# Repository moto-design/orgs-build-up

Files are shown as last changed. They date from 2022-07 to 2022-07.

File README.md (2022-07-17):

# ORGS Build Up

Build up of the ORGS BMW R100GS motorcycle.

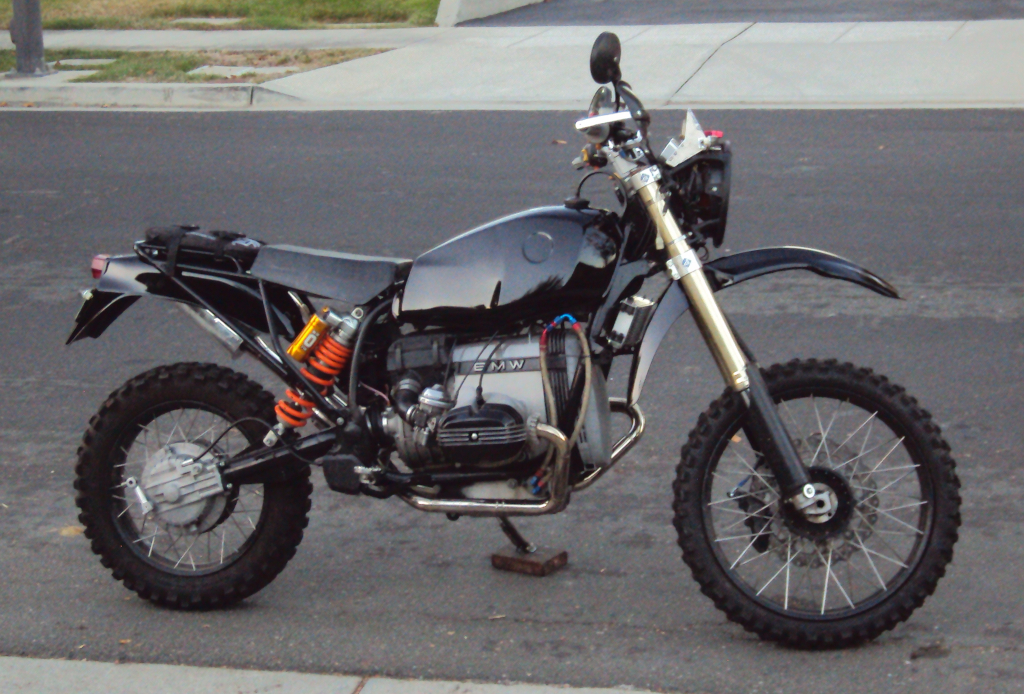
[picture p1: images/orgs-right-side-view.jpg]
ORGS


## Licence & Usage

All files in the [ORGS Build Up Project](https://github.com/moto-design/orgs-build-up), unless
otherwise noted, are covered by the
[Fabricators Design License](https://github.com/moto-design/orgs-build-up/blob/master/fabricators-design-license.txt).
The text of the license describes what usage is allowed.

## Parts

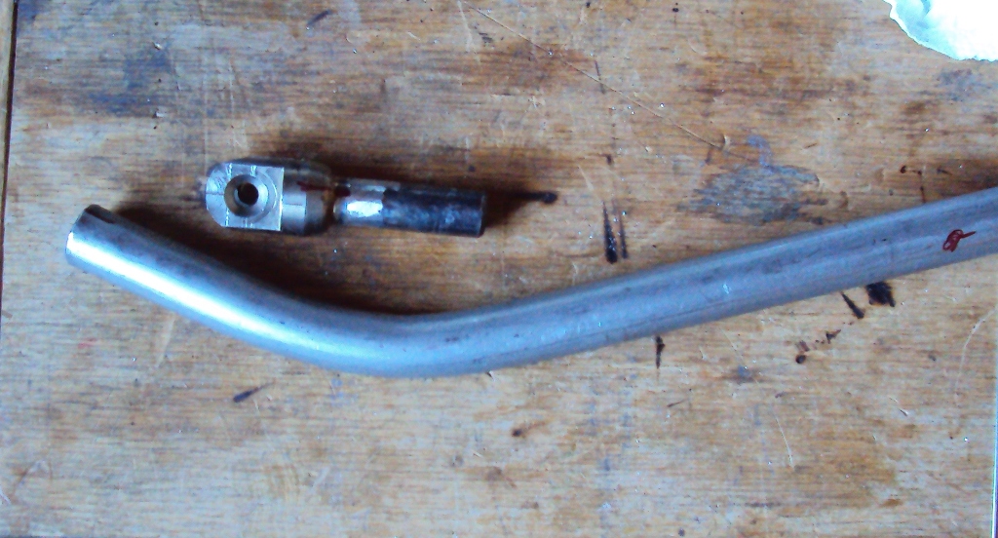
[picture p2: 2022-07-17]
images/50-sidestand/stainless-parts.jpg

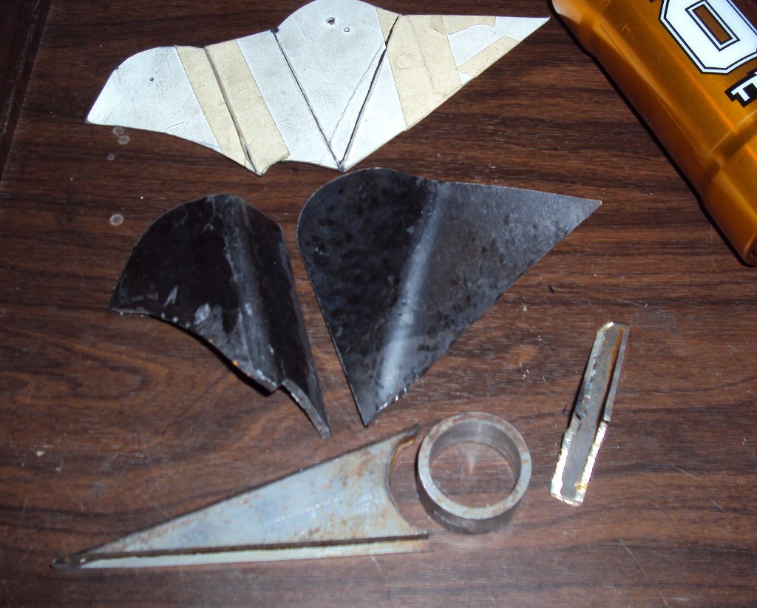
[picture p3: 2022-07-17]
images/32-shock-mounts/mount-parts.jpg

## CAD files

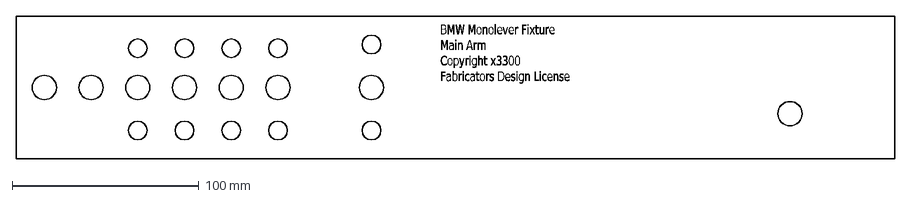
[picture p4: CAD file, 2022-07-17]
images/28-swingarm-fixture/main-arm.dxf
BMW\~Monolever\~Fixture Main\~Arm Copyright\~x3300 Fabricators\~Design\~License

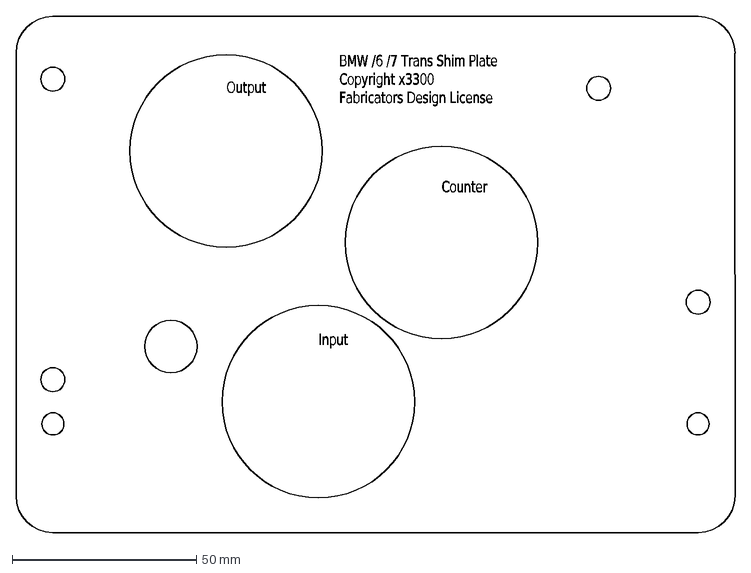
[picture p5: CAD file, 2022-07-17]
images/23-trans-rebuild/bmw-trans-shim-plate.dxf
Input
Counter
Output
BMW\~/6\~/7\~Trans\~Shim\~Plate Copyright\~x3300 Fabricators\~Design\~License

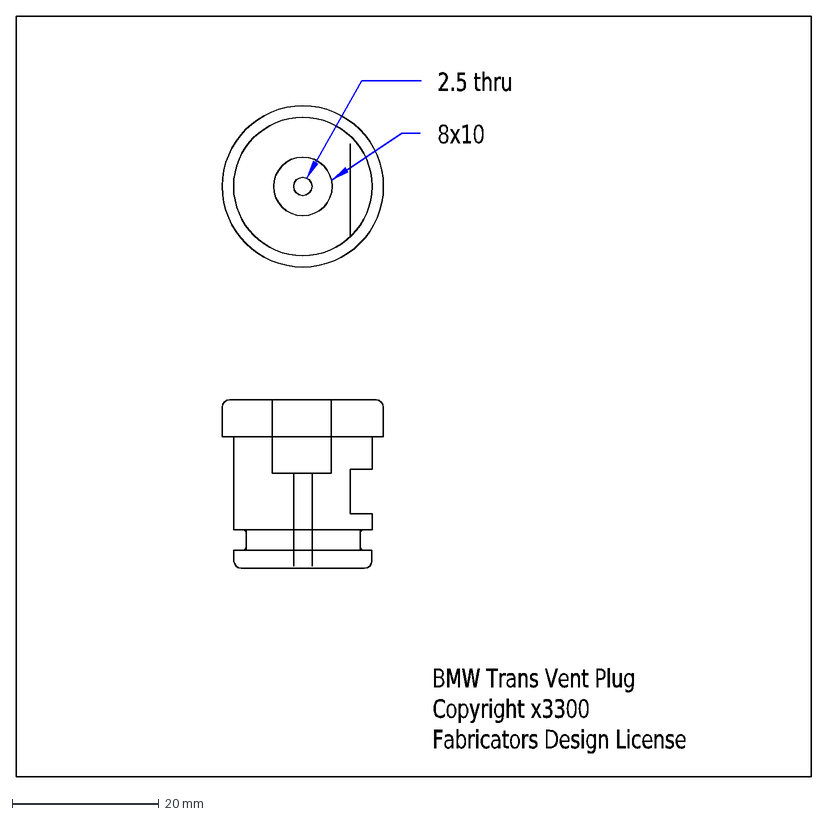
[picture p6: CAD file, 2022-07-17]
images/24-trans-vent/bmw-trans-vent.dxf
8x10
2.5\~thru
BMW\~Trans\~Vent\~Plug Copyright\~x3300 Fabricators\~Design\~License

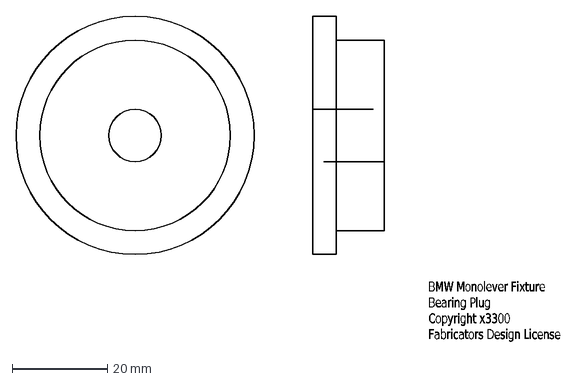
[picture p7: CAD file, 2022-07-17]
images/28-swingarm-fixture/bearing-plug.dxf
BMW\~Monolever\~Fixture Bearing\~Plug Copyright\~x3300 Fabricators\~Design\~License

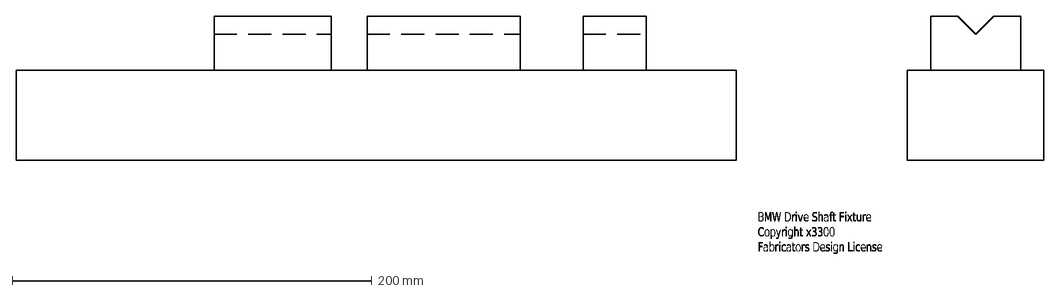
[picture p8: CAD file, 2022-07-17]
images/30-shaft-extension/shaft-fixture.dxf
BMW\~Drive\~Shaft\~Fixture Copyright\~x3300 Fabricators\~Design\~License

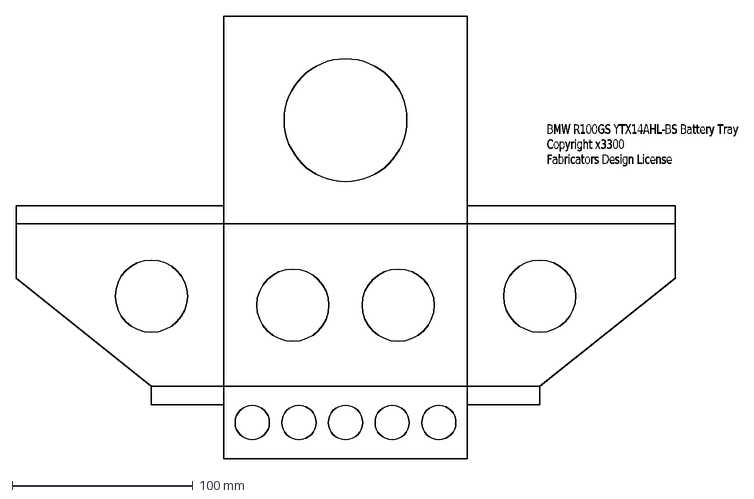
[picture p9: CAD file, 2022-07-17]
images/33-battery-tray/battery-tray.dxf
BMW\~R100GS\~YTX14AHL-BS\~Battery\~Tray Copyright\~x3300 Fabricators\~Design\~License

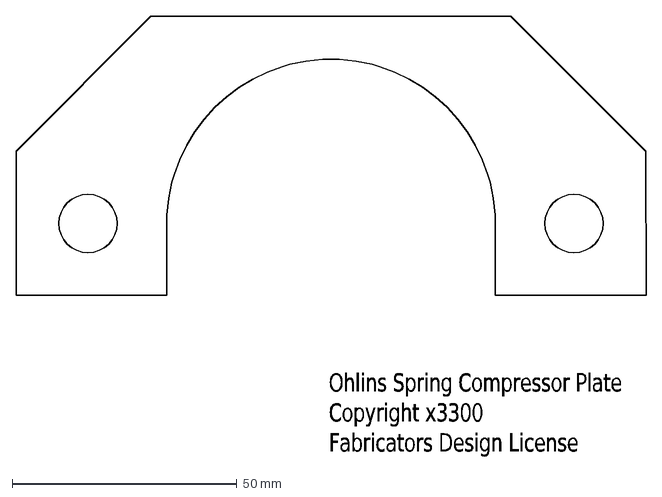
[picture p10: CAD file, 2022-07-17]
images/34-rear-spring/ohlins-plate.dxf
Ohlins\~Spring\~Compressor\~Plate Copyright\~x3300 Fabricators\~Design\~License

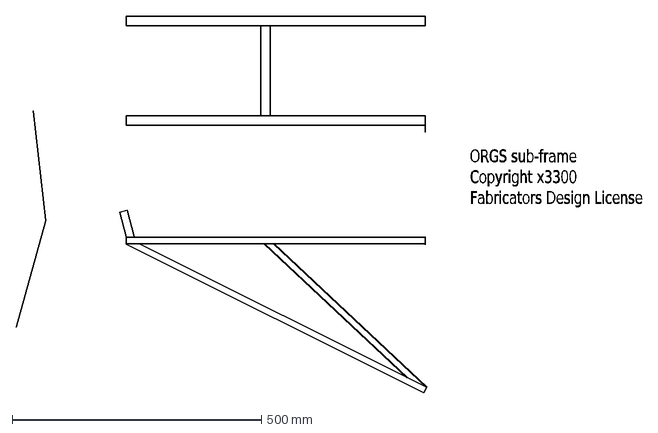
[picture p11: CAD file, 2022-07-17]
images/35-subframe/subframe.dxf
ORGS\~sub-frame Copyright\~x3300 Fabricators\~Design\~License

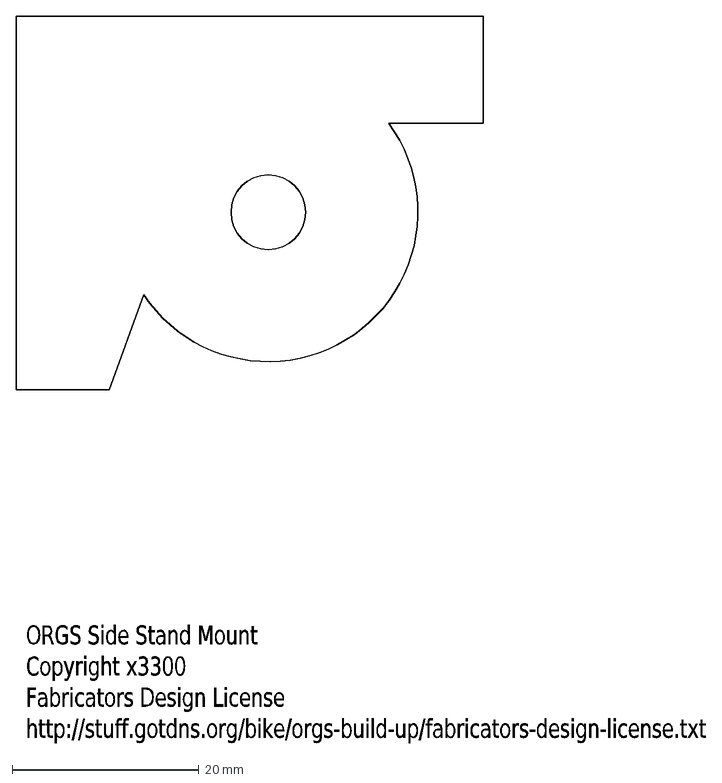
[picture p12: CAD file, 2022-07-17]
images/50-sidestand/side-stand-mount.dxf
ORGS Side Stand Mount Copyright x3300 Fabricators Design License http://stuff.gotdns.org/bike/orgs-build-up/fabricators-design-license.txt

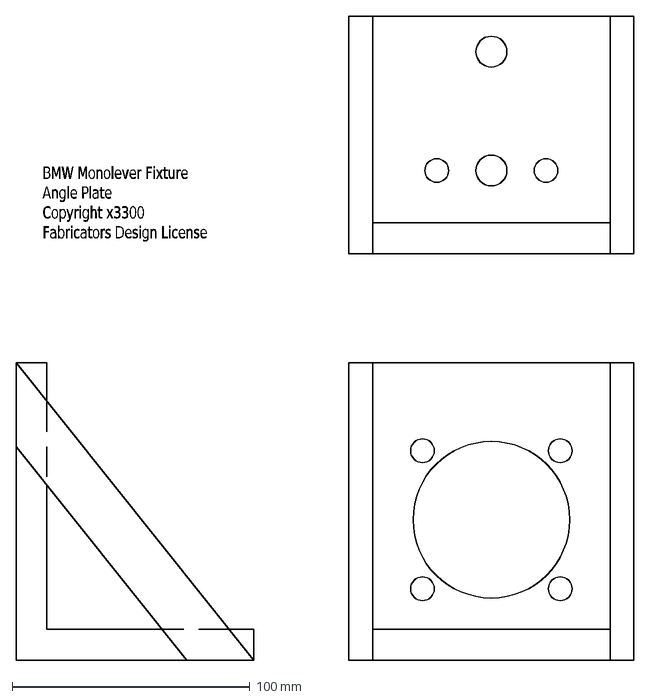
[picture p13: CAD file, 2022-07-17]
images/28-swingarm-fixture/angle-plate.dxf
BMW\~Monolever\~Fixture Angle\~Plate Copyright\~x3300 Fabricators\~Design\~License

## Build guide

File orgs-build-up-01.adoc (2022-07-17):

:url-bmw-frame-gussets: https://www.advrider.com/f/threads/bmw-frame-gussets.638795/
:url-frame-gussets-svg: https://github.com/moto-design/bmw-frame-gussets

:imagesdir: images
:linkattrs:

:notitle:
:nofooter:

= ORGS Build Up - Page 1

[big]*The ORGS Build Up Project*

*Page 1*

*x3300, Mar 6, 2010:*

Hi everyone,

I have really enjoyed the stories of other airhead bike build up projects, so will be posting mine, the build up of ORGS my Off-Road GS here.

I have a good general idea of what I want, but you'll have to follow along as the plan in my head unfolds. My intention is for ORGS to be a bike I can take on the highway and ride all day long for several days to get to a destination, say Moab, Baja, or Copper Canyon, spend a week or so doing some hard riding on unmaintained back roads, then make it back. I want it to be able to take a wipeout without a lot of damage, or cost to repair. That was a drawback of my GSPD. Windscreens, body panels, handle bars, etc. break and cost a lot.

As a base to start with I have bought this '92 GS with 27,000 miles:

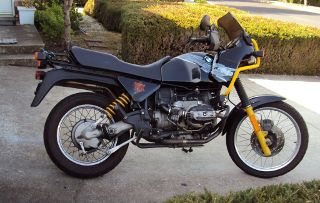
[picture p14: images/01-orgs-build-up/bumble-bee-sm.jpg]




And I got this run down '92 PD with 52,000 for parts:

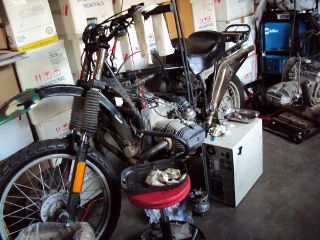
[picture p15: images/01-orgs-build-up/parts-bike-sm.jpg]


The first thing I'll work on is to get the frame in order. I took a day to strip the parts bike down. Here is what is left that I'll start to craft into ORGS. It looks like a chicken to me:

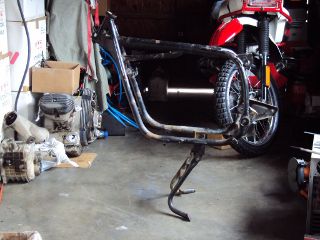
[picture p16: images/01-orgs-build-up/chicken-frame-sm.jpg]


I studied some photos of the frame upgrades done by various projects, and came up with these paper patterns, then cut them from metal I bought at the scrap yard:

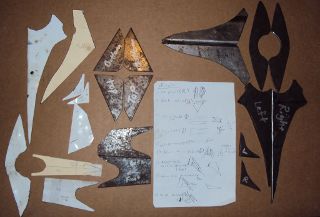
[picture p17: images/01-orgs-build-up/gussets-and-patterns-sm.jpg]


It took a lot of work to get those gussets cut out using a pneumatic cutoff tools.

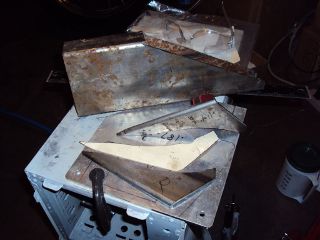
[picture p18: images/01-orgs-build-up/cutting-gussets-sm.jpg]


I made a digital scan of the finished gussets and I'll make some vector graphic data from them which can then be used by anyone interested to program a CAD controled plasma cutter. What took me several days will be able to be done in a few minutes.

Update:

I put the vector graphics I have ready here: {url-frame-gussets-svg}[{url-frame-gussets-svg}]

Also, I started a thread dedicated to frame gussets: {url-bmw-frame-gussets}[{url-bmw-frame-gussets}]

-x3300

*Airhead Wrangler, Mar 6, 2010:*

Looks like you've spent about as much time ogling HPN frame reinforcements as I have. If you'd like some more detailed close up shots of their work PM me an email and I can shoot them over to you.

*x3300, Mar 9, 2010:*

Airhead Wrangler, thanks for the offer. I did a fair amount of research for the frame mods, but will certainly welcome any more info or comments I can get.

Something I forgot to mention the other day in my list up of things for this bike is that it must look cool. I can see that costing some money, but for the effort that will go into it I want this thing to look good.

I got up early Saturday planning to get all the gusset welding done, but it went slower than I thought with fitting the gussets, cleaning the joining parts, grinding tungsten, etc. and I could just finish tack welding all the gussets in place by late Saturday night.

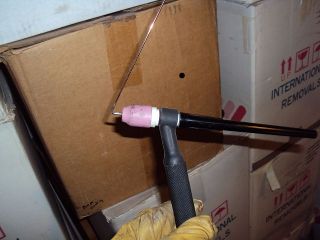
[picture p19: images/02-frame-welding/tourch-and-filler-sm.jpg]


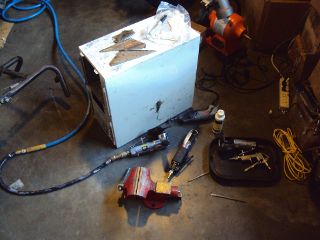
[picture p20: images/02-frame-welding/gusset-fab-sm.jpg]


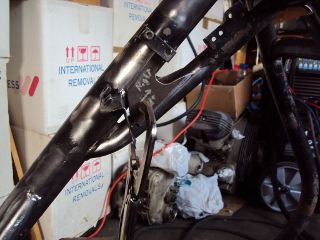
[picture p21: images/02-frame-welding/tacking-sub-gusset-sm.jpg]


It was hard to get the top tube gussets clamped for tacking, but I found that masking tape worked well.

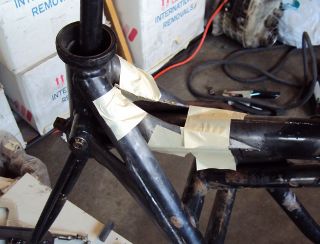
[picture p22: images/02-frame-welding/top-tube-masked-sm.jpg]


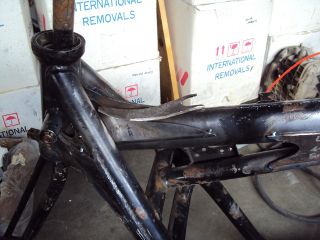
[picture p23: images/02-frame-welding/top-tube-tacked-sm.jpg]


I got up early again on Sunday, thinking I was living the movie 'Ground Hog Day' but could get all the gussets welded up.

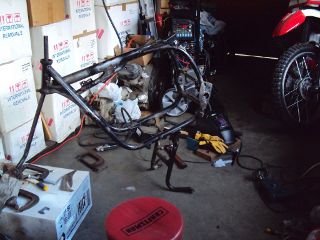
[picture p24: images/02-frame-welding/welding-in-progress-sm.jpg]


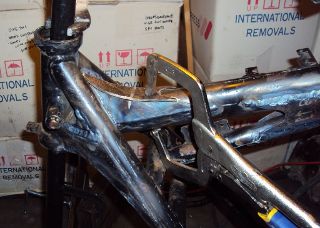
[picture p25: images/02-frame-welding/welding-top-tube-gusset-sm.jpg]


I plan to use an EnDuraLast charging system, so made up some brackets to mount the regulator along the top tube.

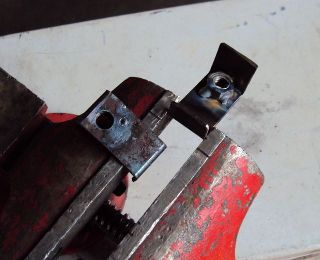
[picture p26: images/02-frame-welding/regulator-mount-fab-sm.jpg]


I am satisfied with the results of the weekend. After two days of serious welding I can certainly say my TIG welding skills have improved.

-x3300

*x3300, Mar 9, 2010:*

I'd like to get some more rear wheel travel out of my paralever suspension, so to get a better idea of the limits I took a few measurements of the shock length at differing swing arm positions. I took some measurements with just the swing arm and final drive bolted up to the bare frame, and some measurements with the fully assembled GS with just the rear shock removed.

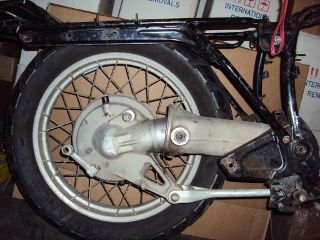
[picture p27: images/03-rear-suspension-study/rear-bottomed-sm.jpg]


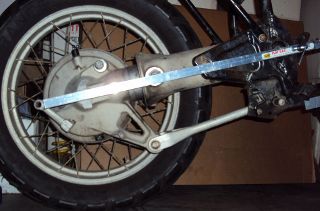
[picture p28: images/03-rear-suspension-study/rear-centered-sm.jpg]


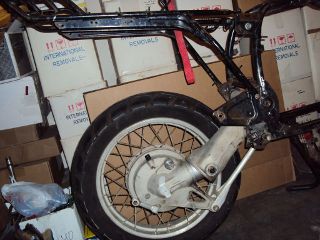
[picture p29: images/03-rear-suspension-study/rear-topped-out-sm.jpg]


Here are my measurements in millimeters:

Code: swing arm topped out 520

drive shaft topped out 505

swing arm centered (zero u-joint angle) 450

drive shaft bottomed ou 402

tire bottomed out (Torance 130/80-17) 392

swing arm bottomed out 387 I found the limiting factor is the drive shaft in both top-out and bottom-out. I could hear the drive shaft rubbing, but because the bike was fully assembled I couldn't tell if the rubbing was from the yokes contacting, or from the drive shaft rubbing on the inside of the swing arm.

To get a ratio for shock stroke vs. wheel travel I measured the change in the distance between the sub frame and the center of the final drive when the swing arm topped out and the tire bottomed out and got 280mm.

travel/stroke = 280 / (520 - 392) = 2.18

So as just a rough limit, between the extremes of when the drive shaft starts rubbing the wheel travel will be:

(505 - 402) * 2.18 = 224mm = 8.8"

Some specs I found for the stock GS say it has 180mm (7.08") of wheel travel, so it seems reasonable to assume that there is no way to add more than 44mm (1 5/8").

I want to do some more study of the u-joint angles and to understand what is rubbing at the extremes. I also have to check if my shock body (Fox twin-clicker) can take a longer shaft, and what parts are available for it.

-x3300

*BALSEY, Mar 11, 2010:*

I like were your going with this .On Sat. I bought a 78' R80/7 with similar plans of resurection. I have an 83' R100,(bought new) that I would be replacing. Too nice to convert. I like the detail in your fabrication.Keep it coming!

*x3300, Mar 13, 2010:*

Thanks for the encouragement BALSEY, I'm glad someone can appreciate my efforts.

During the week I did some cleanup on the frame. As far as I know, dirt bikes don't have passenger foot pegs, and I think this thing really looks out of place, so off it went.

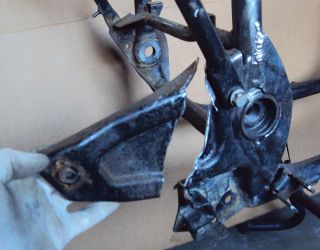
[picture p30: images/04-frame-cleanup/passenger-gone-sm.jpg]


I'll make a custom fork lock. I'm thinking something like the old Harleys had that used a padlock, but using a brake disk lock. Anyway, for now I got rid of that thing also since it doesn't fit into my plan.

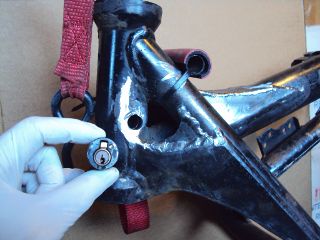
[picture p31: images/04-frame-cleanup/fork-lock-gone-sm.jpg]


To make room for the EnDuraLast voltage regulator on the top tube I cut off the existing bracket that the starter, horn, and load shedding relays mount to. I made up a new relay bracket from a piece of 7/8" square tube stock that I cut length-wise. This photo shows how I set the voltage regulator mounts and the relay mount.

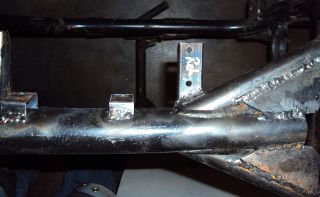
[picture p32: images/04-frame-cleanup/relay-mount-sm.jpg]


Just as a preview of things to come, a package arrived this week with this very cool thing inside. I put it up on the shelf for later. I'll need to make a rear mount for it, as the original mount won't fit with the rear top tube gussets I added to the frame.

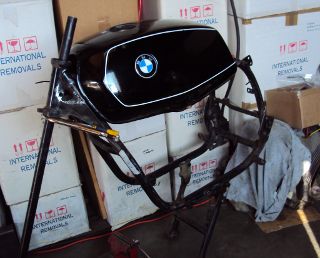
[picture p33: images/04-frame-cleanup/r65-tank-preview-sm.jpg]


-x3300

*Stagehand, Mar 13, 2010:*

I love your work. I would only take issue with the assertion that a GSPD cant take hits without expensive damage. A few good tumbles gets rid of all the weak parts and after that you have to grind shit off to remove it

Other than that, I cant wait to see where you go with this.

You going to keep the stock front end?

You really gonna make that poor paralever go another inch? you sadist!

*Airhead Wrangler, Mar 13, 2010:*

Stagehand said:

I would only take issue with the assertion that a GSPD cant take hits without expensive damage. Click to expand...

Well, compared to a proper aircooled dirtbike, it can't. My definition of a dirtbike is that you can dump it several times per day of riding without anything more than a few scrapes and scratches. GSPDs and any other beemer are heavy enough that when they get dumped, parts either come off or get bent, cracked or otherwise mangled.

This begs the question: what do you have planned for protecting the cylinders? Anything more substantial than the stock bars?

*charliemik, Mar 13, 2010:*

I'm gonna enjoy this. I always wanted to do this to an airhead. I think there's a lot of room for creative improvement.

*x3300, Mar 13, 2010:*

I've done another creative improvement over the last few days. I wanted to lower the pegs and move them back some so I made up these brackets that weld to the bottom of the existing foot peg brackets.

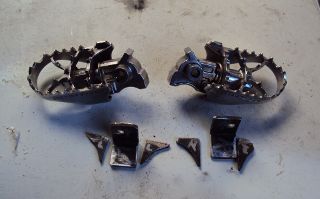
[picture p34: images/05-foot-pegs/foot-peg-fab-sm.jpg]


Because of the brake pedal just below the right foot peg there was a limit to how far down and back I could go. I think to do any more than what I have done would need to have a bolt-on foot peg bracket which could then be removed to service the brake pedal. As it is, I needed to grind back some of the existing brake pedal bracket to allow the brake pedal to drop down (rotate more) to clear the new foot peg bracket. I also needed to grind the brake pedal dirt guard to make clearance for the new bracket. Both these mods can be seen in this photo.

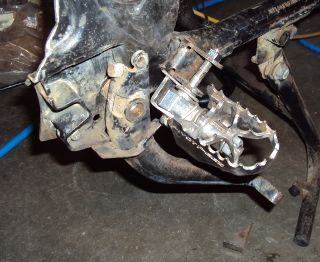
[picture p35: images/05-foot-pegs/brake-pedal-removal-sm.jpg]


The left bracket was relatively easy compared with the right. Here are the finished mounts.

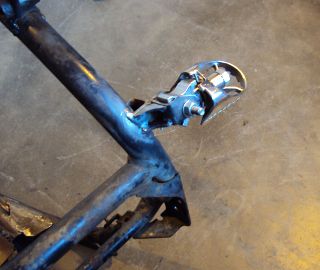
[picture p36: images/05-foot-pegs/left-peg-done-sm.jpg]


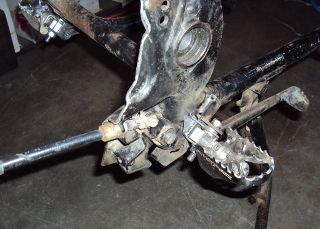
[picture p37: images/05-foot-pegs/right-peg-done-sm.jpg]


-x3300

*Zebedee, Mar 14, 2010:*

... I was born a ramblin' man

Nice work so far X

*x3300, Mar 20, 2010:*

Airhead Wrangler, I'm thinking to make some custom crash bars. I'll relocate the oil cooler and side stand, so that will simplify the design. I'll most likely just put some stock ones on there at first until I get the custom ones made up.

Stagehand, those stock GS forks were out of date even when the bike was new...

I did a lot of minor things since the last post, but only a few worthy of a writeup. To mount the R65 tank I needed to weld the front tank mount back on the down tubes, but it needed to be positioned a little higher since the frame gusset was in the way. I used a bubble level to get it positioned for welding.

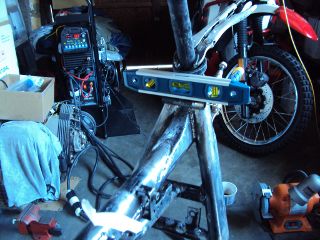
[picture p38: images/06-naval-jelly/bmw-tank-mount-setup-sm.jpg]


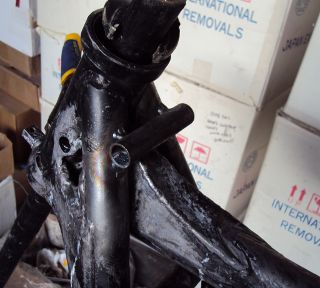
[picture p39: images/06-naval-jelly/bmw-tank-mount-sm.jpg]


The parts bike that the frame came from had sat in a garage near the coast for a few years and had a lot of rusting. I went over the frame with a wire wheel mounted in an electric drill, then with a few applications of Naval Jelly. In general, I was happy with the result.

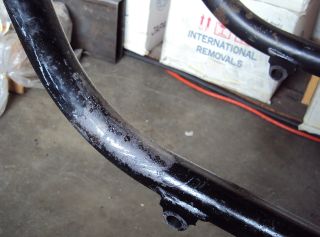
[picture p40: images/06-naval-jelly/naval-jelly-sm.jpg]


-x3300

*x3300, Mar 27, 2010:*

In my last post I mentioned I'd been working on a lot of minor things, and now they've added up to be something to report. Whenever I went down to Baja I always had some envy of those dirt bikes. I tried, but just couldn't keep up. They had such nice suspensions compared to the GS.

Some time ago I got these CRF250R forks off ebay.

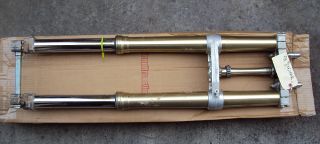
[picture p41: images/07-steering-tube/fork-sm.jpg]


All the CRFs, 125, 250 and 450, use the same fork with minor changes in spring rate and valving.

Here is what I found when I compared the GS to the CRF:

Code: R100GS CRF250R difference

wheel base 1513 mm 1477 mm -36 mm

steering stops 90 deg 90 deg 0

bearing 28x52x16 30x51x15

tube length 168 mm 192 mm +24 mm

rake 28.0 deg 27.5 deg -0.5 deg

trail 100 mm 125 mm +25 mm

triple offset 37.5 mm 24.0 mm -13.5 mm

fork lead 38.0 mm 32.0 mm -6.0 mm

total offset 75.5 mm 56.0 mm -19.5 mm

In the table, total offset = triple offset + fork lead, which is the distance the wheel's center is from the steering axis.

Here is my first attempt at adapting the CRF forks on another bike.

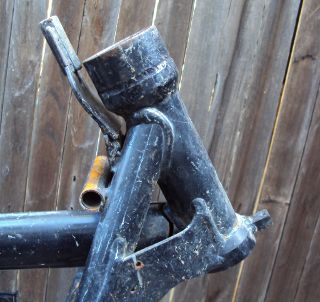
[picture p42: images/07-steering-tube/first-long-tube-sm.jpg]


I just added on another 25mm to the top of the steering tube and fitted some 30x52x16 bearings. It was a relatively simple mod, and it worked out OK, but there were several problems with it.

Because of the shorter offset and the higher front end the trail was jacked way out. It carved around turns and was really stable on the highway, and I found I really didn't need a steering stabilizer. It seemed tiring to ride through tight twisty stuff though, and was also hard to turn when stopped with a lot of weight on the bike.

Another big problem was the loss of steering angle. The lower triple would hit the frame at the down tube gussets. I really missed those extra few degrees. It was very hard to do slow technical riding. When you need to turn into the falling bike to keep it up. There was just no way... I've seen some similar adaptations that put a spacer between the lower bearing and the lower triple clamp. That would allow more steering angle, but would raise up the front end.

Anyway, my list for ORGS was:

90 degree stop to stop steering angle About 110 mm trail Minimize ride hight

The solution I came up with this time was to fit another steering tube that would mount the CRF triple just ahead of the original steering tube, a pretty radical mod.

I found a hydraulic cylinder tube and a chunk of 2.5" round stock at the scrap yard that I though wold work. The OD of the hydraulic cylinder tube measured 65.0 mm. Here is the plan for the tube ends that would take the CRF's 30x51x15 bearings.

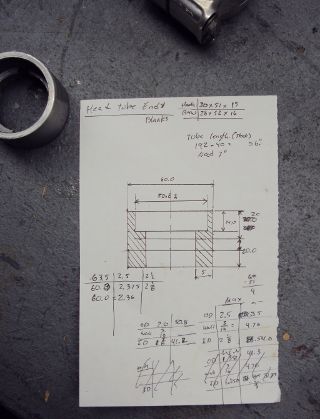
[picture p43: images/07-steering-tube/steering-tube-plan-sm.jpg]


And here is the hydraulic cylinder tube, and the finished tub ends.

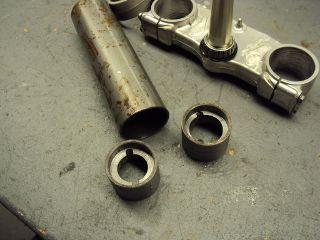
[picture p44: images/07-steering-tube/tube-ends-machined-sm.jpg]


To fit the tube length I just assembled the bearings and tube ends in the triple clamp and marked off how long I needed it.

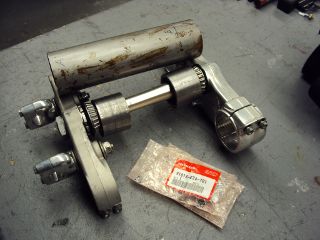
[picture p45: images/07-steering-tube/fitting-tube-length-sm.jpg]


Here is the finished head assembly. You can see here where I had filed grooves in the lower triple clamp to get more steering angle clearance on the old bike.

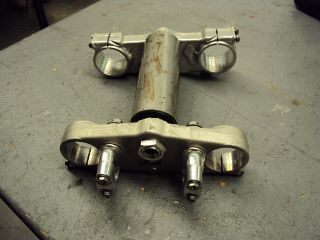
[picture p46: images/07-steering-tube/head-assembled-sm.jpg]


Based on measurements and trial fittings I figured I needed to set the bottom of the new tube about 40 mm in front of the original tube to give me enough clearance between the lower triple and the frame down tubes to get the 90 degrees of turning I wanted. The original steering tube diameter is 60 mm, and the new tube 65 mm, so if the new tube goes 40 mm in front of it I would need to cut the old tube where the new and old tubes intersect, then weld on the new tube.

But wait, I also needed to set the new steering tube at a steeper angle than the original to get the reduced trail I wanted. I did a some calculations based on the geometry of the two bikes and found I needed to cut about 6 mm less off the top of the old tube than at the bottom of it.

Now the new tube is a perfect cylinder, but the old tube has a reduced center section, a complicated intersection to figure out... I only had one chance to do the cut, so I wanted to be pretty sure it would be right. I figured I'd better have a pretty good handle on that intersection before cutting. I used a graphical geometric calculation to get the four intersection points of the very top of the tube, the top and bottom of the reduced section, and the very bottom of the tube.

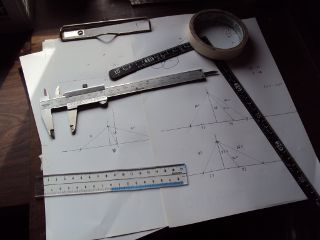
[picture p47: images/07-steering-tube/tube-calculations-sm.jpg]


Being a bit nervous, I made a trial cut and checked the fitting.

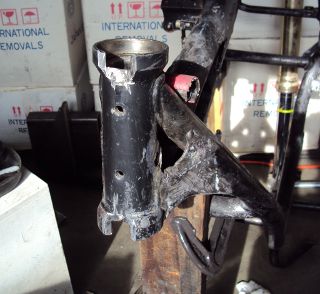
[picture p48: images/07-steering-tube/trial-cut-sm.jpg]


Then I transfered the intersection points to the tube then sketched in the rest of the cut.

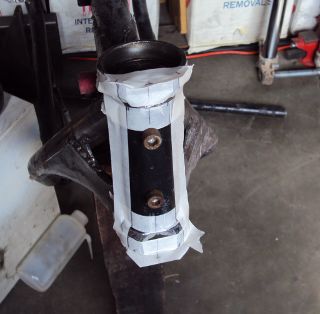
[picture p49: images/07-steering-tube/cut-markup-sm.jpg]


Then did the final cut.

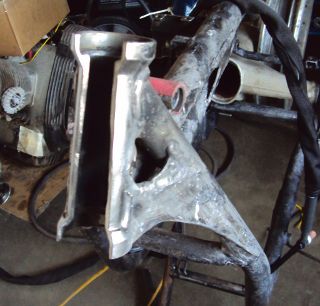
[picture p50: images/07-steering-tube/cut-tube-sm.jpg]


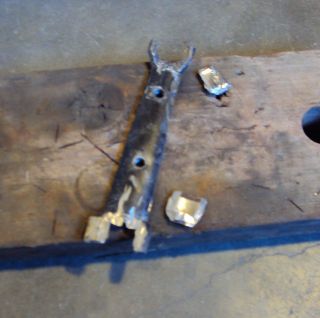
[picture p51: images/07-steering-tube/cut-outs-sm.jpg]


I put the swing arm and rear wheel on the bike to use as a baseline to align the new steering tube, then ground the sides of the cutout with an air grinder until the two pieces mated up and the new tube was aligned with the rear wheel.

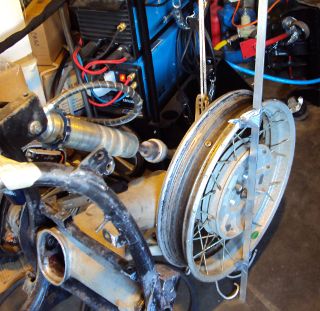
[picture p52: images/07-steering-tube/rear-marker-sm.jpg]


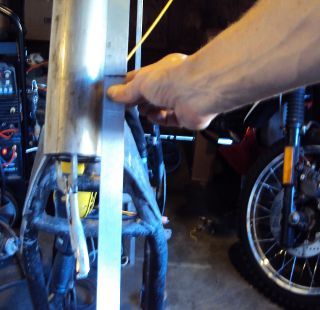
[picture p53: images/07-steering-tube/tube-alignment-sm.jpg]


Then, with the two straight edges aligned I tacked the new tube in place.



After a lot of checking and a break for coffee I welded the new tube on.



To add strength and cover the hole of the old tube I made some gussets from 1/8 stock.









I wanted to mount a Scotts steering damper (http://www.scottsperformance.com), and the stock CRF triple just doesn't look very cool, so I bought an Applied Racing Stabilizer-Ready triple clamp (http://www.appliedrace.com) that had the same offset of 24 mm as the stock CRF.



To fabricate a tower for the damper I got a 3/8-16 brass screw, coupler and jam nut. I cut the head off the screw and filed the sides down until the screw just fit into the slot of the damper arm.



I welded the coupler to a bracket made from 1/8 flat stock, then welded that to the top cover. I needed to chase the coupler threads with a tap after welding it.





This shows the steering angle is close to 45 degrees. The limit is in the damper, not the steering stop.



I'll need to weld some small shims to the frame so the steering stop will hit it before the damper reaches its limit.





It was a big mod, but I am very satisfied with the result. This photo just doesn't present what it looks like, it looks really cool in person.



I'm really wondering how it will ride, and where it will crack if it does.

-x3300

*Airhead Wrangler, Mar 27, 2010:*

Oh man. This is getting savage. Not going to be putting THAT frame back to stock. Nice work.

*Stagehand, Mar 27, 2010:*

Wow :huh :eek1

That is pretty amazing. Savage is an excellent word.

*bgoodsoil, Mar 27, 2010:*

holy crap man. I've seen plenty of fork swaps but nothing like that.

*x3300, Apr 3, 2010:*

Given the will, there is a savage way!

I've been pushing to get all the frame welding done so I can move on to other things. I added two gussets to the shock mount to give it a better connection to the frame.



A big box arrived by air freight from Germany.







I really liked having the big tank on the PD. I've done 1000 mile days with it where I just needed to fill-up a few times. A big tank is really nice when you go off into the mountains for a day or two and don't need to carry extra cans. I'll have this big tank for trips, and use the R65 tank for local riding.

I got the more expensive nylon tank that can be painted. I figured it would be a better investment, as I can repaint it when it gets scratched-up or when I want to change the color scheme.



I made up this pattern in the lower right for the front tank mount bracket.



I don't have a photo of the unmounted bracket. I fabricated it out of 1/8" flat stock and drilled a big hole in it.

I used a piece of welding rod and a bubble level to align the two brackets on the frame, then tacked the brackets.







The welded brackets look a little flimsy. I'll add another support running from the inside of the down tube to the bracket, but I don't have any stock of that size. I'm thinking 1/8 x 1/2 will work good. Here's how it looks with the tank.



For the rear mount I made up these bungs with a M8 x 1.25 threaded hole.



I bolted the bungs up to the tank to get the alignment for welding.

As seen in the photo, the tank mounting tangs are not quite even. I thought the reason for the difference was that the two gussets were not aligned, but after welding I checked it and it was the tank. I should have done the check before welding it up. I can fix the tank by shaving some material off the the one side, or gluing a spacer on the other. I can fix the frame by either welding a washer on the low side, or grinding the high side.



I used some thin sheet aluminum to make a heat shield between the bung and the nylon tank, but the tank got hot enough for the nylon to melt a little when I did the tack weld. After welding up the bung I chased the threads with a tap.



As I mentioned in an earlier post, I got this black R65 tank off ebay. I really like the shape.



I like the lines of the tank and this GS long seat.



The R65 tank is longer than the HPN tank so I made up this adapter plate. Whenever I want to use the R65 tank I'll need to bolt on this adapter.



The R65 uses a hanging swing type of mount in the rear, but there was just no way to get that working with this modified GS frame, so I took the old mounting hardware off the tank and made up a new mounting plate from 1/16" flat stock that will bolt to the frame adapter plate. Here I have the new mounting plate clamped to the tank and ready for tack welding.



Once, when I was a kid, I was working on the tank of my Hodaka Super Rat and the fumes in the tank ignited. It was a minor explosion, but scared the hell out of me. Since then every time I work on a gas tank with heat I do this check.



Here's the plate tacked to the back of the tank.



Here is the modified tank bolted to the adapter plate. I just have some spacers that were handy in there to check the fit. I'm thinking to make another smaller set of M6 bungs to weld to the adapter plate.



The fitted R65 tank.



-x3300

*sraber, Apr 3, 2010:*

Damn fine work! and good tank check

*ChromeSux, Apr 3, 2010:*

On the subject of welding gas tanks, a guy i know welds on motorcycle gas tanks quite often, one day while he was doing one i ask him how did he get them clean and free of fumes, he said he did not worry about it, he just emptied the tank and ran a Argonne gas line into the tank while welding and that would prevent any fumes from igniting.

*NOTICES*

All ORGS design materials are relesed under the Fabricators Design License.
Copyright x3300

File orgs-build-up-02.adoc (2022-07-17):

:url-bmw-frame-gussets: https://www.advrider.com/f/threads/bmw-frame-gussets.638795/
:url-frame-gussets-svg: https://github.com/moto-design/bmw-frame-gussets

:imagesdir: images

:notitle:
:nofooter:

= ORGS Build Up - Page 2

[big]*The ORGS Build Up Project*

*Page 2*

*Stagehand, Apr 3, 2010:*

120 ppm @ 120degF i think is the flash point of 87 octane gasoline.

Thats all that matters.

*Beemerguru, Apr 3, 2010:*

Great job and wonderful vision....now when the frame is done..you ARE going to send it off to the Frame Man to straighten it out aren't you?

*x3300, Apr 11, 2010:*

Beemerguru, I aligned the steering head when welding it on, and it looked OK after I was done, so shouldn't need any further alignment.

If some frame alignment was needed, well, this project is not about sending things out. It is about creation, about taking an idea, forming a concept, and realizing it in metal, rubber and plastic. A sturdy fixture to bend the frame into alignment would just be one of the many fixtues and jigs that will be made for this project.

I found some thin sheet stock and cut two shims from it to set the steering stop to just before where the steering damper hits its limit.



The Applied Racing triple clamp I bought mounts the damper in the reverse direction, so I needed to buy a stepped arm that drops down to clear the damper body. I made this puller to pull the old arm off.



As I mentioned in my last post, the front HPN tank mounts I made up seemed too flimsy, so I added a brace to the inside of the existing bracket. I found some rusty stock that I cut to fit.



Then welded it on. It is amazing how the triangle makes it really strong, I guess the whole bike could be picked up by just one mount.



To fix the botched rear HPN tank mount I cut the welds of the miss placed bung with an abrasive cut-off wheel, ground off all the old weld, then re-welded the bung at the correct hight.



I made up this set of smaller bungs with M6x1.0 threads for the R65 tank adapter.



I needed to set the bungs up so that the bottom of the tank will clear the heads of the bolts that mount the adapter to the frame.

After I figure out what I'll do with the front seat mount, etc., I might simplify things here by cutting up this adapter such that I can just weld it to the frame.



-x3300

*canderson88, Apr 13, 2010:*

Something wicked this way comes!

*anonny, Apr 13, 2010:*

Cool build I'm in

*x3300, Apr 24, 2010:*

I've been busy on a lot of different things since my last post, and could finally get something together worth reporting. Just to let you know where I am going here is a cardboard box 'studio' photo of the result.



These are adapters I found I needed to get all the front wheel related parts I wanted to use mounted up to work together.

Here is a list of the parts:

  Fork:           Honda CRF250R
  Wheel:          BMW R100GS
  Axle:           Honda CRF250R
  Brake Disk:     Ducati snowflake (320mm)
  Brake Caliper:  BMW R1200RT (4 piston)

I really like the convenience of the stock GS tubeless wheel. It seems really strong, and I can repair a puncture without removing the wheel from the bike. Plus, I just need to carry a small tire plug set and an MTB bicycle pump to do repairs.

The GS axle is bigger than the CRF's. Here is what I measured:

                 R100GS   CRF250R  difference
  axle diameter: 25.0 mm  20.0 mm  -5.0 mm

I didn't want to bore out the CRF fork ends to accept the GS axle since that would need to be done again if the fork ever needed to be replaced. I looked into fitting a bearing that would have the OD of the GS wheel and the ID of the CRF axle. The GS uses a number 6005 bearing with dimensions 25x47x12. The closest standard bearing with the proper ID and OD is a 6204, with dimensions 20x47x14. The GS wheel bearing bore is really just deep enough for the 12mm bearing, and I didn't think it the good to use the thicker 14mm 6204.

I did find that some Suzuki motorcycles use a 20x47x12 bearing in the transmission, but those wouldn't be sealed, so wouldn't be appropriate for wheel bearings.

I would need to make some custom axle spacers to fit the GS wheel between the CRF fork, so in the end, the solution I came up with to fit the bearings was to make a set of stepped spacers that extend into the wheel bearing to adapt the GS wheel bearing to the CRF axle.



I found some kind of stainless round stock at the scrap yard that I though I could use. I made the OD of the new spacers the same as that of the stock GS spacers so I could use the GS bearing protectors on the new spacers. This shows the stock GS axle and spacers on the right, and the CRF axle and custom spacers with the GS bearing protectors switched over on the left.



To get the correct width for each of the new spacers I mounted the GS wheel in the fork with the CRF axle nut screwed on the axle until the outside of the nut was flush with the end of the axle, then positioned the wheel so that the rim was centered between the fork legs. Careful measurement gave me 15.5mm on the right, and 27.0mm on the left for the spacers.

This shows the CRF axle with my new spacers and GS wheel bearings.



I had done a 320mm disk conversion on my PD earlier, so had a good idea of what I needed to get the disk mounted. You can read my write-up of the PD conversion here:

http://www.advrider.com/forums/showpost.php?p=6638696&postcount=214

The Ducati snowflake disk has an offset of 9.67mm, but an additional spacer is needed to get the disk far enough over so that the spokes won't hit the inside of the caliper. Also, it seems to me that if the disk is closer to the fork leg there will be less stress in the caliper mount.

I took the springs out of the fork so I could compress it down the check how thick a spacer I needed to get 2mm clearance between the widest part of the fork upper and the outer surface of the brake disk buttons. I measured that about 11mm would work.

I was lucky and found a 1/2"x4"x4" aluminum cutoff at the scrap yard. I didn't have any proper lathe mandrels so I drilled a hole in the stock and pressed in a piece of scrap steel that I turned down and center drilled. That big square spinning around was a little intimidating at first, but I showed it who as in charge, and quickly got it turned down to its 100mm OD.





These photos show how the axle spacers and disk spacer work together to position the wheel centered in the fork, and the disk as far to the left as possible.





To get the brake caliper setup I just positioned the caliper on the disk to where it looked good. It seems a little high in this photo, I thought it would put too much stress on the upper mount.



The geometry of the adapter needed is not simple. I took some measurements, but mainly made the finished piece from a template.

At first I was trying to make templates from thick card stock, but that turned out to be difficult because of the irregularly shaped parts. I hit on this idea to use a thin piece of clear PETE plastic and a sharpie marker.





Once I got the template and knew the size of the adapter I scrounged around at the scrap yard and found a block of aluminum I could use.

The adapter needed two reliefs on the outside for the fork mounts, and one big one on the inside for the caliper. I just sketched the reliefs onto the template to give about 2mm clearance between the adapter and other parts, then just transfered the sketchings to the piece when doing the layout.

This shows the caliper and inside relief, along with some of my fabrication notes.



I plan at some time to make a proper mechanical drawing of the adapter for use by anyone interested.

The three big holes on the side are to reduce weight and give a better appearance. I didn't plan on those at first, but once I got it machined and mounted up it looked like a big bulky hunk of metal sitting there so I added the holes. I think it looks a lot better, and is significantly lighter. The holes are not quite lined up because I positioned them in the center of the thickest parts to give maximum strength.

This adapter ties together a Honda fork, a Ducati disk, and a BMW caliper...



Here is a top view. The 2mm relief gap between the adapter and caliper is in the shadows of this photo, but looks narrow and gives a really good effect.



It was a lot of work to design and machine the parts, but I am very happy with the result. The axle spacers are stainless, which won't rust, and the caliper adapter has a really cool 'one-off' look to it.

-x3300

*Zebedee, Apr 25, 2010:*

Nice work

John

*SamH, Apr 25, 2010:*

Wow, Fantastiic work.

*Mr. Vintage, Apr 27, 2010:*

Nice job!

*Solo Lobo, Apr 27, 2010:*

Really nice stuff going on here

*x3300, May 1, 2010:*

I'm almost done with all the frame mods and starting to work on various things around the frame. So that I can do some of the measuring and fitting I set the old engine and trans from the parts bike into place. The header pipes were all rusted up so I went over them with a wire wheel and it really improved the look. I guess they will rust up again soon though.



I found that when climbing up steep mountain back roads (1st and 2nd gear stuff) in hot weather the engine of my PD would overheat. After a bit of looking around at automotive plumbing catalogs and such I ended up ordering an Earl's Temp-a-Cure oil cooler, some -6 Perform-O-Flex stainless hose, and a few Swivel-Seal hose ends that would mate the cooler to the threaded holes in GS oil filter cover plate. Other aftermarket parts makers have similar offerings.



I sized the cooler to be a bit bigger than stock and to fit in the space behind the front fender. This photo shows the stock GS cooler compared to the new cooler. It is thicker, and the front has about 30% more finned area.



I wanted to have the front fender so I could properly fit the cooler. I looked around for something with a modern look to it and settled on a Acerbis for the limited edition black CRF450R. I'm hoping the aerodynamics of it will be good at highway speeds.



To mount the cooler I decided to use two aluminum plates that would mount above and below the cooler to stabilize it and offer some crash protection. The lower plate would mount to two brackets that would be welded to the front frame tube. The lower plate would need two big holes to pass the fittings on the bottom of the cooler.



As a first attempt I made these plates from 1/8" flat stock. I machined out the top plate mainly for looks, but also to make it lighter.



The frame brackets needed to be narrow enough to fit between the cooler fittings. I still need to cut off that horn mount, but will need to wait until the engine is out next.



The lower plate then mounts to the frame with four counter sunk screws.



To connect the hoses to the GS filter plate I bought two M12x1.5 'fuel pump' hose ends (Earl's PN 849092). These have the same thread as the stock GS banjo bolts. I also bought some clear 3/4" heat shrink tubing to put over the hose to keep grit out.

The filter cover plate had a recess that the banjo sealing washer fit into that can be seen in this photo.



I filed down the edges of the recess to make a flat sealing surface for the new hose ends.



Here is how the new fittings connect up with the GS filter plate.





Here is my 1/8" lower mounting plate with some temporary hardware. After getting this far I found the lower plate seemed too flimsy, and I felt the plate would eventually crack from fatigue. There is about 67mm between the inner frame mounting screws and the outer cooler mounting screws, with a big hole between them.



As a solution I welded some 90 degree angle stock on the sides of the lower bracket. This photo shows that work in progress. On the bottom I needed to grind away some clearance. With hind sight, I think a better design would be to just make the lower plate from 1/4" stock. The current one should work OK, but I may make up a new one.



I made up this set of spacers from 1/2" round stock to fit between the cooler mount tabs. I machined a flat on two sides to accept a 10mm wrench. I also use two washers between the cooler tabs and the mount plates to space the plates away from the top and bottom of the cooler. The cooler is then sandwiched between the plates to stabilize it.



I was concerned that I would not be able to remove the front engine cover with the oil cooler mounted, but I found that the cooler and hoses are far enough forward that there is plenty of room.



Here's a side view showing the clearance between the cooler and the fender as mounted.



It seems like the front fender will obstruct most of the airflow to the cooler. I'm thinking I'll cut out some of the fender to allow the the air to flow into the cooler, and maybe make some shrouds that attatch to the sides of the cooler to duct some more air through it. I'll wait until later when the bike is ridable and I can do some air flow testing before doing that though. I also need to add the heat shrink cover, and I am thinking I to shorten the hoses by 1/2" or so.



-x3300

*Stagehand, May 1, 2010:*

Yah you'll want airflow through the fender,, but you dont have to cut it off if you can just drill some holes in it.

*x3300, May 8, 2010:*

I had one of the Enduralast alternators from Euro MotoElectics on another bike, and can recommend it for the improved charging. The down side of the kit is the wiring. It just provides some general instruction, a handful of electrical connectors and some wire. You are left up to your skills to get it working.

The combined rectifier/regulator comes from a two wire Ducati system, and it just doesn't mate into the two component Bosch diode board + regulator system of the GS very well. Here's the rectifier/regulator from the kit.



I wanted the wiring for the new alternator to be reliable and clean so figured I'd need to make up some kind of custom wiring harness. I started by taking measurements of the existing engine wiring harness and whatever else would be needed to connect up the new regulator and came up with this harness drawing.



I think for maintenance it would be better to have connectors between the regulator and harness so the regulator could be easily replaced, but that would be complicated because the wires to the alternator need a high AC current rating, etc. For reliability I choose to wire the regulator directly into the engine harness.

The result for the most part is a direct replacement for the OE engine harness. The regulator needs switched power on the white wire which has no equivalent in the OE harness. My solution was to run another wire out along side the wires to the main harness connector and put on a blade connector that would need switched power from somewhere. I need to do some re-work on the main harness and I'll add in a new wire from switched power to connect up here.



In my old installation one of the connectors between the alternator and the regulator burned up. It happened on a trip to Baja, and the battery was ruined, so I had to finish the trip with a lot of push starts. I think that the AC current must get really high at times, then any resistance in the connectors will cause them to get hot and eventually burn up. As a quick fix while down in Baja I got some wire nuts from a hardware store. Those worked so well I left them on. Anyway, I want to have some good connectors there to avoid problems. For now, I put in a heavy duty terminal block. I'll attach it to the timing cover with a screw to hold it in place.

-x3300

*x3300, May 15, 2010:*

I'll need a headlight, and I wanted something distinctive, something that said -- off-road.

I liked the the look of the big 8" race lights and figured I'd try to rig something up for street use. Both Baja Designs and Trail Tech make very similar products, an 8" light with a simple frame that attaches to the fork uppers with hose clamps.

I chose the Trail Tech light based solely on Internet photos. Both are so similar that I can't imagine one could be much better than the other. I'd like to hear from anyone who has compared them side-by-side.

Here's what arrived at my door.





This light comes fitted with a single filament 55 watt H1 bulb. This really isn't suitable for a street use headlight. After a bit of headlight study (see here) my idea was to fit a standard H4 (9003) bulb to the 8" shell. The H4 bulb is a dual filament bulb with an off-focus low beam filament and integral low beam mask.

I needed an H4 bulb holder to replace the existing H1 holder so I searched around at the local motorcycle wrecker and found what seemed to be a pretty common H4 light on older Honda motorcycles. The back shell is made of plastic and I figured it would be easy to cut down to make a bulb holder that could be glued onto the back of the 8" light.

Here's the junker compared to the 8".



I took a hammer and a pair of pliers to the Honda light to break away the front lens from the rear shell.

The H1 bulb holder on the 8" light is cast aluminum and held onto the shell by several bent over tangs and a bead of what seemed to be high-temp RTV silicon. I bent the tangs up and cut the silicon away to get the holder off.

Here is the H4 shell set on top of the 8" light.



Using a lathe I cut off the outer part of the plastic H4 shell then turned it down to a good size. Here's a comparison of the two holders with bulbs.



The drawing shows the bulb dimensions I measured:

  H1      = 27.0 mm
  H4 high = 20.0 mm
  H4 low  = 28.0 mm 

The H1 bulb holder places the bulb about 5 mm behind the shell, so to get the H4 high beam filament at the same position that the H1 filament was I would need the base of the H4 bulb about 2 mm in front of where the H1 holder rests against the shell. Anyway, I marked out the cut with a Sharpie pen and started toward it on a bench grinder. I noticed the reflector mirroring started to peal off inside the bulb from the heat of grinding so I switched to a hand file.

Once I started getting close I checked the placement of the bulb by looking through the front lens at the reflection of the high beam filament in the reflector. Because of the reflector's parabolic shape it was easy to see when the filament was at the focal point.

Here's the filed down shell and my bulb holder ready to be glued together.



After all the grinding and filing there was a lot of metal and mirror junk inside the light that needed to be cleaned out. I started by just flushing it with clear warm water, then on the final fill-up I added a tablespoon of household ammonia to help reduce water spots. I was really surprised with the result. A very clean inside and only a few unnoticeable spots.

I got some Permatex Ultra Grey RTV silicon to glue the new holder to the shell. It seems to be very similar to what was originally used to hold the H1 holder on.



Here are a few photos that show the finished headlamp.







Here's the high and low beam patterns on a cardboard target a few feet in front of the bike. Both were taken with the same exposure settings.





The low beam pattern seems pretty good. I'll need to get the bike out of the garage to check how it looks down the road.

-x3300

*x3300, May 30, 2010:*

The frame of the Trail Tech headlamp I bought has four threaded mounts that I thought would be a good place for my dashboard. I wanted to make up something with a minimal look.

I thought a multi-function digital computer would be good to base my dash on since I could get a number of features from a single device. I looked at a few models, and decided on the Trail Tech Vapor. It had most of the features I wanted at a reasonable price.



For warning and indicator lamps I first bought these 12 volt LED lamps which have a built-in resistor and holder, but I had second thoughts about them as they look a little big, so I then bought some bare LEDs and small clip holders that I will try. I'm not sure if I can get the installation of the bare LEDs to be reliable enough. They seem like they will easily get damaged.



I also bought a few heavy duty toggle switches. With all the components on hand I did a mock up of the dash to get the measurements for the top panel.



I went through a few iterations of the layout with components at different positions, etc., until I got to the final layout. I did a mock-up with thick card stock to get the shape of the side panels that put the dash at a good viewing angle. Here's one of my design drawings with a side panel template and a few of the different lamps I bought. The sharp point at the top of the template is to form a kind of glare guard and mini wind screen.



I found some 1/16" 6061 aluminum sheet at the remnant shop that I thought would work well.



After cutting out the rough shapes on a band saw I used a mill to get the parts to shape and machine out the openings for the components.



I used this piece of flat stock as the front mounting bracket. To allow full adjustment of the headlamp I needed to cut out the relief. I made the bracket wide so I can mount a pair of small auxiliary driving lamps above the main headlamp.



Here I have the parts taped together with masking tape as a final check before welding.



Welding the dash panels to the lower mounts.



Here is the finished dash. I still need to wire up all the components, a big job in itself.





I also need to get a key lock switch for the ignition. I'm thinking to hang a bracket down below the dash side panel, but on the inside of the headlamp frame so the key switch is recessed into the gap behind the headlamp.

-x3300

*tileman, May 31, 2010:*

I'm liking this

*Zebedee, Jun 5, 2010:*

x3300 said:

...

I also need to get a key lock switch for the ignition. ...

-x3300 Click to expand...

If you are looking for clean and "simple", have you considered keyless?

I seem to recall one Aussie inmates going that way with his R65 Cafe build

$0.10

Cheers

John

*x3300, Jun 5, 2010:*

Zebedee, keyless sounds good. I often seem to get all saddled up with gloves and everything on to only find my key is deep down inside my pocket.

I'll need to make up some kind of custom seat since the stock GS seat doesn't fit with the frame gussets I added, and also, the shape of the HPN and R65 tanks I have are considerably different from the stock GS tank.

To get some ideas I made this seat mock-up from thin cardboard.



There was a lot of unused space below the seat top, so I thought it would be a good place to store some tools and spare parts. I made up this model to size up a large tool tray.



My idea was for the seat pan to mount on the top of the tool tray. The HPN and R65 tanks are different lengths, so I would need a design that would allow the seat to be used with both. I decided that the tray would stay fixed to the frame, and the pan would have front to back adjustment. Here is the pan mock-up on the tray. The marks in the back show the pan position with the two tanks.



I spent a lot of time measuring the profile of the tanks and cutting and fitting the pan to get a shape and position that I thought looked good. Here's how it fits to the the R65 and HPN tanks.





As I mentioned in a previous post, I wanted to replace the R65 tank adapter I had made with a mount welded directly to the frame. I made up this template for a mount that could be used for both the R65 tank and the tool tray. The front of the tool tray will have a bracket welded on that sticks out and bolts to this frame mount. The bracket on the tank and the bracket on the tray will stack together and then bolt to the frame with two bolts.



Here's the bracket cut out and bent. It will get some threaded bungs welded on after it is welded to the frame.



When I got the 1/16 aluminum stock for the dash I got enough for the tool tray also. I cut the panels then bent the bottom panel on a sheet metal brake. With a bit of filling the side panels were even and mated to the bottom with a good fit.



Here's the bottom panel in position. I left some extra on the front to be trimmed while fitting the front panel.



I used this card stock template to get the geometry of a cut out that would be needed to clear the frame.



Here's the tray taped together for a final check before welding.



To weld the panel edges square I used this piece of angled scrap. The vice-grip is set as a stop to register the panel in position.



The panel is set in position.



Then some tack welds.





And tack the other edges.



Then the final welds.



I trimmed the extra off the top of the panels, then used a disc sander to get the top of all the panels even. This shows how the tray fits into the frame and its position with respect to the tank mount, which is welded to the frame here.



Here's the tray so far.



I put in a lot of detail in this write-up, and the piece isn't even finished... I still need to make the two small panels to seal the frame cut-outs, make up the front and rear mounts, and make up a mounting system for the seat pan.

After the tray is done then I can start on the seat pan then move on to the seat pad and cover. I've been gathering up seat design info for the next steps. I found some good info here http://www.diymotorcycleseat.com

-x3300

*notarat, Jun 5, 2010:*

Awesome write up thus far!

Subscribed

*NOTICES*

All ORGS design materials are relesed under the Fabricators Design License.
Copyright x3300

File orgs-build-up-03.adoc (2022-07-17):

:url-bmw-frame-gussets: https://www.advrider.com/f/threads/bmw-frame-gussets.638795/
:url-frame-gussets-svg: https://github.com/moto-design/bmw-frame-gussets

:imagesdir: images

:notitle:
:nofooter:

= ORGS Build Up - Page 3

[big]*The ORGS Build Up Project*

*Page 3*

*Benjamin M, Jun 12, 2010:*

Great thread dude. Especially interested in the high/low beam mod that you've made to the TT 8" headlight..

Any progress made since your last post?

Cheers, Benjamin

*RemcoR, Jun 12, 2010:*

Looks like a great project! My respect for your drive to do so many things yourself.

I am working on something similar, but I have the advantage some work has been done for me and there is a bit more stuff for sale over here.

I bought this 1992 R80GS with a Siebenrock 1000cc kit and a WP 48mm usd front fork (foto attached). After that I have put on a mono seat on a self made shortend rear frame, with a smaller battery, a BSM stainless steel exhaust with a good Y-pipe, a UNI open airfilter, an oilcooler, a ring to enlarge the oil pan and self made bash plate instead of the pan, an inversed brake lever at the back, a HE 320mm front brake disk, adaptor plate and caliper. I am trying to reduce weight everywhere (mainly using the angle grinder). The dashboard consists only of a Nuvi 510 GPS, the instrument lights and a bycicle speedometer. A second one and a roadbook holder will follow. The taillight consists of LED's and the front light (classic G/S basic front) has an xenon light.

I am busy refurbishing the carbs, timing chain and rectifier (same as your setup) and I want to mount some subframe for a set of saddle bags (no cases for me). I have an appointment with a suspension specialist because I also want to raise the rear end (so please keep us posted here, the road I want to take is to shorten the bar underneath the swinarm and with that straightening the rear angle of the swingarm) and I am interested in your frame reinforcement drawings.

Regards, Remco

*x3300, Jun 13, 2010:*

There seems to be a lot of popcorn munchers out there...

I got some more work done on the tool tray, but it's still not finished yet. I made up some corner pieces to complete the cut-outs I needed to clear the frame. Here I have the first one tacked in.



After I got it all welded up I did a backyard hydrostatic leak test. This photo shows two cross tubes I added to make the sides more rigid and to work as part of the seat pan mount. They also make nice carrying handles.



I made up a single wide front mount that bolts to the R65 tank mount I now have welded on the frame, and two rear mounts that have slots that go onto the sub-frame cross tube as seen in the later photos.



I wanted to have a design that would have the seat, tool tray and battery theft proof with a single lock. My idea was to have the rear of the tray slide onto the sub-frame cross tube with the front of the tray elevated. The tray would then pivot around the sub-frame tube to bring the front down to its mount, and front would then be bolted to the frame. The seat covers those bolts, and then the seat will have a bracket of some kind (TBD) to allow it to be locked to the frame.

My solution will certainly work, but now that I have it fabricated I feel it could use some improvement. The rear mounts seem like they will wear fast and get sloppy. Also, there is too much side to side flexing of the tray so the rear mounts move side to side. I'll think about some way to improve it.



I have a Rick Mayer solo seat on my PD that I find comfortable on long rides so I decided to try to incorporate the same general shape into my seat, but on a much trimmed down scale. To start, I made up this seat pan template that could support the seat I'm thinking of.



I found this 16 gauge aluminum sheet from a discarded air conditioner cover or something that I thought I could use. I thought the alloy was 3003, but it seemed to crack easily when shaping it, so it might have been something harder. I laid out the sheet with a Sharpie pen.



The shape of the pan didn't allow me to shrink the material to form this corner so I cut out a wedge shaped section with the plan to weld the seam together. Here I have the seam tack welded. As I was shaping I didn't do any annealing, and some cracks resulted which are visible in this photo at the top of the seam. I welded up the cracks with the seam.



For added strength I made this 6061 under pan to weld onto the bottom of the seat pan.



Here it is welded to the bottom of the pan.



Here's the seat pan so far. Its a little difficult to see, but the photos show how I put both a lengthwise crown and a cross crown to stiffen up the top of the pan.





I'm really happy with the result of the tool tray and seat pan so far. Before I started on them I was wondering what I could do and wasn't quite so sure how to progress, but now they are almost finished with just a few more bits of work to do.

-x3300

*x3300, Jun 29, 2010:*

The design and fab of the tool tray plus seat pan assembly has taken some time, but I'm almost finished. In my design the tool tray bolts down to the frame, with the seat pan then attached to the tool tray.

I made up these aluminum hooks to weld to the bottom of the seat pan. The hooks are intended to slide under the tubes I have welded into the tool tray and hold the seat pan firmly to the tool tray.



I had previously welded a solid sheet of aluminum to the underside of the seat pan to form a stable base for its mounting to the tool tray, but I decided to remove that sheet and instead use two pieces of aluminum angle to act as sub frame rails. The hooks get welded to the rails.



Here's how the rails fit onto the tool tray tubes. The sides of the tool tray fit into the groove between the rail and the hook to hold the pan from moving side to side.



I then welded the rails onto the underside of the seat pan.



To add some rigidity to the sides of the seat pan I made up end panels from flat sheet and welded them to the seat pan.



Once I got the rails and end panels welded in I did some trial fitting with the R65 and HPN tanks to find out how much of the underside hooks to trim. Here is the finished seat pan with the hooks trimmed.



Here's a back view. I just laid a string of spot welds to hold the end panels in.



I still need to arrange some kind of latch and lock mechanism. I found this nice looking draw latch at McMaster-Carr which looks like I can mount the arm vertically on the rear end panel and the strike below on the tool tray to draw the seat pan firmly down onto to tool tray and lock it into position.



To get a feel for how much and what kinds of foam I'll need I glued on a few layers of packing foam I had on hand.



The seat pan mount is functional, but I'm not entirely satisfied with it. I don't really like the rail and hook solution I came up with. The pan is hard to put on, doesn't really fit well, and the rails aren't very strong so won't offer much theft protection. I already have a reworked design that I think will function better, but my plan is to move on to unfinished things like the seat foam and cover.

-x3300

*x3300, Jul 3, 2010:*

After a bit of looking I came across the Master Receiver Lock 1473DAT at my local auto parts store that I thought I could make work as a fork lock. The package included 1/2" and 5/8" receiver pins and a single lock.

Here's the 5/8" pin and lock.



I used an abrasive cut-off wheel to cut the pin so that the fork upper would hit the lock squarely when locked on. I ground off some of the chrome plating near the end of the pin then welded it onto the frame head tube so that there would only be a few degrees of fork movement.



Here's how it looks when locked. Its not super secure, but will prevent an opportunistic roll away theft.



I can also lock it in the other direction, but it is harder to access the lock and there's about 30 degrees fork movement.



-x3300

*x3300, Jul 5, 2010:*

I've started to focus on getting the electrical system in order, which will be a fair amount of work in all. I've already got the voltage regulator harness done as reported in a previous post. I'll also need to rebuild the main and sensor harnesses, which will include some mods to each. The rear harness is in good condition, and I think I can use it as is with maybe some changes to the terminals for a different tail lamp and turn signals. The dash electronics need to be designed and wire up, and an overhaul of the bean can which has a sticky advance is needed. I haven't decided on the tail lamp and turn signals, but I do know I'll try to use LED units for those.

I needed to wire in an engine temperature sensor for the Trail Tech computer I have in the dash. I figured the cleanest way was to have the sensor lead run under the left carb and hook into the existing GS sensor harness then go up through the main harness to come out up near the steering head.

I took some measurements of the GS sensor harness and came up with this harness design diagram. The connector I used for the temp sensor between the sensor harness and the main harness is a Molex .062 2-pin connector.



Here is the stripped sensor harness, a Trail Tech temp sensor I'll use, and a Trail Tech V300-48 sensor extension cable. The extension cable isn't long enough to reach from under the carb to the steering head so I'll need to extend it with some wire in the main harness. For the sensor harness end I just cut it to the right length and soldered on Molex connector pins.



Here's the finished sensor harness with a new connector for the oil pressure switch.



I'll put the temp sensor under the rear left valve cover nut. I plan to hook up an oil temp sensor later.

-x3300

*Mr. Vintage, Jul 6, 2010:*

Lookin' very good. Clever fork lock design too.

*x3300, Jul 11, 2010:*

The main wiring harness needed some modification to accommodate the Enduralast voltage regulator and other accessories I wanted. I made up this diagram to work from.



At the dash I wanted dedicated power and ground for auxiliary lights, grip heaters, etc., and to have those switched by a relay in series with the existing load shedding relay so that the accessories would also be shed when the starter motor was running.

I found the existing tach signal compatible with the trail tech computer so no harness mod was needed for that, but I did needed to run temperature sensor leads down to the sensor harness as I mentioned was needed in my previous post.

The parts bike didn't have a usable main harness, so I found one on ebay from a seller in Israel. Here's what arrived. It's generally in good shape, but much of the wrapping tape is falling apart.



It seems after time the tape adhesive dries up and what's left is just glue dust and loose fabric. Where the fabric is really loose dirt and grit enter into the harness.

As I was cutting off the layers a lot of sand and dust was coming out and I imagined the previous owner hauling out in top gear across the vastness of the Israeli desert with a huge cloud of dust trailing behind.





I cleaned up the bare harness and all the connectors with compressed air and a tooth brush.

To start with the mods I put the harness in position and installed the various components it connected up with.



I choose to use 3M Scotch Super 33+ and Super 88 vinyl tape for the rebuild. The 33+ is a little thinner and good for binding and prep work. I used the thicker 88 for the final wrap layer.

I've used these tapes before for harness rebuilds and was satisfied with the result. The finished look is different than the original GS fabric tape, but I think it gives an acceptable look.



For spicing wires together I bought several sizes of brass tube from a local hobby shop. I cut a small piece off with a hacksaw and finish the ends with a file then crimp and solder the connection.



Here's where I tapped into the existing green 'switched power' in the harness to add in the new voltage regulator power lead.



And the finished connection between the main and engine wiring harnesses.



Here's what I was faced with in the front. A lot of existing stuff, and a lot of added stuff for the dash. It took a while to get everything sorted out.



I could get that thing under control though, and here's the finished harness laid out.



With the harness wrap finished I installed it on the bike and started on hooking up all the connections. This shows how the voltage regulator and relays fit with my custom mounts and the rebuilt harness.



To get the things under the front cover in order I needed to take apart the bean can and figure out why the advance was sticking. I won't go into the details of that since its well reported elsewhere. I found some rust on the moving parts of the advance mechanism and figured that was the problem. I cleaned it up and put some high temp grease at the moving parts.



This shows how I ran the alternator output wires and how I attached the terminal block to the timing chain cover.



In the front there was a lot of extra wire since I no longer have the faring nor instruments. It took a while to get it routed and bundle so it wasn't too ugly. The headlight covers most of the bundles.

I'll do some more work up here later as I continue on the dash wiring.



-x3300

*rediRrakaD, Jul 11, 2010:*

Thanks for sharing and inspiring. Nice build. Cheers, S.

*Zebedee, Jul 11, 2010:*

rediRrakaD said:

Thanks for sharing and inspiring. Nice build.

Cheers,

^^^ what he said ^^^

Don't ya just hate it when these folks make it look so easy ...

John

*x3300, Jul 24, 2010:*

I've been working on the dash wiring and a lot of other miscellaneous things around the bike since my last report. I'm hoping to get the dash wiring done this weekend.

Here's what I've been dealing with.



All custom stuff for the most part. I made up this diagram to work from. It doesn't yet include the instrument lights.



On the dash I'll have switches for two independently switched auxiliary front lights, a switch for the headlight low beam, and a switch for the hazard flasher. I have a hazard capable flasher unit, but I still need to figure out what kind of switch it needs and how to wire it in. I'll also have a rotary pot for variable power grip heaters. I'll cover the design of these in another report.

To power the GPS unit I'll have a 5 volt source going to a USB Mini-B plug. This will plug directly into my GPS. I'll also have another 5 volt source going to a USB Series A receptacle to power auxiliary devices like a cell phone charger, a Walkman, or an NiMH battery charger.

Here's what I'm working on for the USB power, I'll have two separate LM7805 linear voltage regulators for the supply. I had some USB cables kicking around that I'll cut up and solder to the LM7805's output.



Just for reference, a typical pinout for USB connectors:

  pin 1 red   = +5 volt
  pin 2 white = data -
  pin 3 green = data +
  pin 4 black = gnd

I'll just leave the white and green data lines unconnected. The regulators I chose can source 2 amps each, but to do so for very long will need good heat sinks on them. I'll screw them down directly to the aluminum dash for that.

-x3300

*NordieBoy, Jul 24, 2010:*

x3300 said:

Just for reference, a typical pinout for USB connectors:

  pin 1 red   = +5 volt
  pin 2 white = data -
  pin 3 green = data +
  pin 4 black = gnd

I'll just leave the white and green data lines unconnected. The regulators I chose can source 2 amps each, but to do so for very long will need good heat sinks on them. I'll screw them down directly to the aluminum dash for that.

-x3300 Click to expand...

Some gps's'ss's's need the data lines shorted or something so they don't go into mass storage mode.

*Zebedee, Jul 26, 2010:*

`NordieBoy said:

... gps's'ss's's ... Click to expand...

Bless you, Nordie.

  bless you, English/Kiwi = Gazuntite, 'merkin

Oh, and keep up the good work X3300

*Mr. Vintage, Jul 30, 2010:*

x3300 said:

To power the GPS unit I'll have a 5 volt source going to a USB Mini-B plug. This will plug directly into my GPS. I'll also have another 5 volt source going to a USB Series A receptacle to power auxiliary devices like a cell phone charger, a Walkman, or an NiMH battery charger. Click to expand...

What is a walkman?

Lookin good....

*x3300, Aug 14, 2010:*

NordieBoy, pin #4 of the USB Mini-B is normally not used. Some newer Garmin units use pin #4 to detect if the unit is connected to a computer or a charger. Chargers have pin #4 grounded, and computer cables have it open. My unit (Oregon) has an option (Spanner) to ask the user what to do on connection.

Here's the connector pinout:

  USB Mini-B pinout

  pin 1 red   = +5 volt
  pin 2 white = data -
  pin 3 green = data +
  pin 4 brown = n/c
  pin 5 black = gnd

For now I'll use Spanner mode. I'd like to have a connector that has pin #4 grounded, but I haven't found anyway to do this other than by buying a Garmin charger and cutting off the connector.

I found these cables from Argent Data Systems that have a lead for pin #4, but unfortunately, the angle of the connector won't work with my Oregon.



Here's how I soldered up the 5 volt regulators.



And the finished supplies ready for installation. I applied some heat sink compound and screwed the heat sinks down to the underside of the front dash mount bracket.



I decided to try using the individual LEDs for the dash instrument lights. I soldered on 1K ohm resistors to each LED and used heat shrink tube on all the connections to insulate and strengthen.

All I have to show the construction is this blurry photo.



And here are the finished dash lights. I used the OE light harness and cut off the existing bulbs then soldered on my LEDs. The photo also shows my notes on polarity and wire color of the different lights.



Here's the dash powered up. I pressed the LEDs into their clip holders from the back with a few drops of 'super glue' to keep them from popping out.



It seems the 1K resistors will give a good brightness. I'm thinking a night dimmer would be nice to have, but I'll wait until I get some real use before deciding to make something.

I found the dash as designed really too tight underneath. It was hard to install and wire up the components. It would be nice to have some more space below the top panel to ease maintenance.

-x3300

*nella, Aug 14, 2010:*

The dash looks great!

*x3300, Aug 21, 2010:*

I noticed that the output shaft of the trans was a bit tight to turn, and I had intended to go through it, so decided it was as good a time as any to take the trans apart put some new parts in. I won't go into much detail of how to do a rebuild since it has been well reported elsewhere.

I have this flange puller from Ed Korn's Cycleworks. I don't think it would be to hard to make something though.



Here's a side view of the puller.



With the flange off I used some heat and a plastic mallet to get the cover off and pull out the parts.



The new parts; 5 shaft bearings, some seals, a neutral switch, the critical shifter spring, a 1st gear bushing, and a 688 bearing. The front input bearing was OK, so I decided to not replace it. I also put in a new cover gasket.



I took the shift mechanism apart to replace the critical spring. I put a witness line on the cams with a Sharpie marker.



I also replaced the plastic detent roller with a 688 roller bearing as seen here. 688s are used for in-line skate wheels, so easy to find.



I used this puller to get the bearings off.



Here's the output shaft disassembled. I took it down this far to machine a groove to accept a circlip that will hold the front bearing on, a standard mod for these transmissions.



The circlip is an external 17x1. The DIN 471 spec gives a groove diameter of 16.2 mm, so I only needed to remove 0.8 mm off the shaft diameter.

Here's how I mounted the output shaft on a lathe to turn the groove. I ground the width of a standard carbide cutting tool down to about 1.5 mm, then made the cut with the right edge of the tool 18 mm from the bearing shoulder (17 for the bearing, and 1 for the circlip). The shaft was pretty hard, but I went slow and could make the cut with the carbide tool. I've heard of using a grinding attachment to grind the groove.



To make up a plate for shimming the bearings I mounted the trans cover on a mill and used the mill's DRO and an edge finder to get the relevant cover dimensions.



Here are the measurements I came up with.



And the resulting shim plate drawing to work with.



Here's the plate bolted to the assembled trans ready for shimming.



The bearing end clearance of each of the three shafts needs to be set using shims. The proper shim thickness is determined by measuring the depth of the cover hole that accepts the bearing, the thickness of the plate, the thickness of the cover gasket, and the height of the bearing above the plate.

Code: gap = cover + gasket - plate - bearing



Anyway, I could get it all shimmed up and reassembled without much worth reporting.



-x3300

*bgoodsoil, Aug 21, 2010:*

Seriously man, what do you do for a living? This isn't the work of some n00b like me.

*maverick, Aug 21, 2010:*

Nice work dude, following with interest. You are certainly very talented

*NOTICES*

All ORGS design materials are relesed under the Fabricators Design License.
Copyright x3300

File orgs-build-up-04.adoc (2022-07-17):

:url-bmw-frame-gussets: https://www.advrider.com/f/threads/bmw-frame-gussets.638795/
:url-frame-gussets-svg: https://github.com/moto-design/bmw-frame-gussets

:imagesdir: images

:notitle:
:nofooter:

= ORGS Build Up - Page 4

[big]*The ORGS Build Up Project*

*Page 4*

*fishkens, Aug 21, 2010:*

Wowza. So far you've done a few things that I've done or had on my list for a long time (relocated oil cooler with earles fittings, Acerbis nylon tank, new headlight, gauges, etc.) and about a million things I never dreamed of. I'm fascinated.

Thanks for the write up.

*AirheadGS, Aug 22, 2010:*

Nice work! Thanks for posting the dimensions for the shim plate. You might want to put in a night mode on the LEDs now. I changed out all my bulbs to LEDs and the high beam turned out to be too bright for night, and I still have not fixed it.

*x3300, Aug 28, 2010:*

The Trail Tech computer I'll use has its own reed switch speed sensor, so I won't need the trans speedo cable. I also wanted to arrange a trans vent hose to both avoid the OE hollow trans bolt and to have the ability to put the hose into the air box to draw moisture out of the trans when water gets in there from a river crossing or whatever.

I made up this trans vent plug from aluminum. Also shown is the stock trans plug that attaches the speedo cable.



This is an updated trans vent drawing. I haven't yet made one to verify the updates, but I think it should be OK.



I measured the trans hole as 19.0 mm. The design uses a 1/8 NPT hose barb fitting for the outlet, but to keep the plug's profile low I decided to turn the threads of the hose fitting down and just epoxy the fitting into the plug. I put a metric 16 x 2.0 o-ring on the bottom of the plug to keep oil from seeping up and out of the fastening bolt and the top of the plug.

O-rings seal by being squeezed between mating parts, the terms 'squeeze' or 'crush' are generally used here, and is expressed as a percentage of the o-ring cross-section. Generally, for a static cylinder plug like this a crush of around 20%+ is recommended.

The machined edges of the trans, both at the hole's opening and at the edge formed by the cross drilling of the fastening bolt were sharp and made it difficult to install the plug without cutting the o-ring at 20%, so I reduced the crush to about 17% by cutting the groove deeper. I also put a chamfer on the trans opening, but it was still a careful operation to install the greased plug.

Here's the assembled plug.



And the plug installed in the trans.



-x3300

*nella, Aug 28, 2010:*

Very nice work!

Scott

*x3300, Sep 2, 2010:*

There have been a few glimpses in past posts that there is just a bare hub where the front wheel should be. Things finally came together to get that taken care of.



I put in an order and this box arrived.



Inside was a shiny new 21" tubeless rim.



Older rims were marked Akrnot, Spain, but this is marked Behr, Germany. The markings are sand blasted on.



I wanted to make up something distinctive and decided to try some powder coat. A little research told me that polyurethane powder would be well suited for wheels, and I found this 'Black Cat' polyurethane powder from Caswell Plating. I also got a roll of high-temp powder coat masking tape from them.



My first real attempt at powder coating. I was really happy with the result. I masked off the bearing bores to keep the coating out and applied two heavy coats.



I made up this bearing driver to install the wheel bearings in the hub.



To prepare the rim for coating I needed to sand blast the polished finish off the new rim. It was a hard thing to bring myself to do considering the time I have spent polishing GS rims, but once I got the rim in the sandblaster and pulled the trigger I went at it with determination. The blasted rim.



I sent out inquiries for R100GS spokes to both Buchanan's Spoke & Rim and The Devon Rim Company. I received a very queer reply from Buchanan's recommending spokes threaded on both ends and 80 nipples per wheel.

Doug Richardson of Devon Rim seemed to understand what I needed and even with shipping from the UK and a currency exchange fee gave me a better quote than Buchanan's. The only difficulty I had with Devon Rim was their inability to do credit card sales. I need to send them a personal check, which I found a bit out of date. All went well though, and these polished stainless spokes arrived in a small heavy package.



The powder coat oven I have access to is not big enough to fit a 21" front rim, so I needed to make up some way to heat the rim to 390 degrees Fahrenheit and hold that temperature for 15 minutes. My solution was to heat the rim with two propane torches while I spun it on a wheel stand. Here's my setup.



I found a discarded bead frame rail in a dumpster that I used for the stand. I just did a very quick fab job cutting the sections and welded them together. I laced four spokes into the wheel, just enough to support the rim as I turned it gently. The torches are propped in position by large c-clamps.

I needed to keep both torches at full to get the rim to come up to temperature. I think three torches would work better.



I used this infrared thermometer from Harbor Freight to monitor the rim temperature.



Anyway, after two coats and lots of spinning I was really surprised at what came out.



After getting the rim coated I had everything needed to start the wheel build. I used copper based anti-seize on the spoke threads and the hub nipple bores.



Lacing the wheel was pretty straight forward. Since the brake caliper is mounted on the left I laced the hub with the hub markings on the right so the markings would be visible as on the original wheel.

To get a close to equal initial spoke length I used this M3 screw with nuts as a depth gauge through the top of the nipple. Also shown here are some grub screws. I ended up not using these. I'll see how things work out without them.



To keep track of where I was I put these marks on the wheel. The tape on the rim with the red circle marks the axial high point. The blue was to mark the rim weld.



Here are the tools I used to build the wheel. A dial indicator, a torque wrench, masking tape and markers.



Here's how I setup the dial indicator. It was a little tiring to bend over to read it though. I put a little grease on the rim to lubricate where the dial indicator plunger slid on the rim. I didn't want to put the indicator on the outside of the rim for fear of scratching that finish.



After I got the radial and axial run-out in control I set the dish with this straight edge.



In the end I had a radial run-out of 0.7 mm and an axial run-out of 0.4 mm. The BMW service manual gives a factory tolerance of 1.0 mm and a service limit of 1.3 mm for both.

Here's the finished wheel with a TKC-80 mounted.



I can now finally after many months roll the bike around.

-x3300

*Padmei, Sep 3, 2010:*

Far out nice rims.

*NordieBoy, Sep 3, 2010:*

Nicely done.

*Gimmeslack, Sep 3, 2010:*

This is frikkin' amazing. Brilliant hillbilly engineering!!

x3300 said:

The powder coat oven I have access to is not big enough to fit a 21" front rim, so I needed to make up some way to heat the rim to 390 degrees Fahrenheit and hold that temperature for 15 minutes. My solution was to heat the rim with two propane torches while I spun it on a wheel stand. Here's my setup.

I found a discarded bead frame rail in a dumpster that I used for the stand. I just did a very quick fab job cutting the sections and welded them together. I laced four spokes into the wheel, just enough to support the rim as I turned it gently. The torches are propped in position by large c-clamps.

I needed to keep both torches at full to get the rim to come up to temperature. I think three torches would work better.

I used this infrared thermometer from Harbor Freight to monitor the rim temperature.

Anyway, after two coats and lots of spinning I was really surprised at what came out.

-x3300 Click to expand...

*rediRrakaD, Sep 3, 2010:*

Once again a creative solution . Thanks for posting. S.

*datchew, Sep 3, 2010:*

black rims and TKC-80's.

I'm seeing a trend developing here. Real nice work so far. I'm enjoying watching.

*One Less Harley, Sep 3, 2010:*

wish I had known you needed a rim as I could have sold you a good used one for half of BMW price. To late as I sent the rim and hub to have a tube rim laced to a GS front hub.

*x3300, Sep 19, 2010:*

I needed to make up a long brake line that routes around the big Trail Tech race lamp.

The R1200RT caliper I'm using had a broken off bleeder, so I figured it would be a good time to fix it. I bought a new bleeder and removed the broken stub with a bolt extractor. I heated the caliper around the bleeder with a torch to expand the aluminum.



I got a few different kinds of hose to make up the brake line. Also shown is the bulk braided brake hose.



I used Earl's Speed Flex -3 hose and Speed Seal hose ends to makeup the line. Details of its use have been covered elsewhere. To get some rigidity in the run between the mount at the top of the fork protector and the line guide I used some stiff plastic hose over the brake line.

When the fork compressed a sharp bend was forming at the upper hose end. I was worried that over time the brake hose Teflon liner may fail here due to fatigue so I used some flexible hose over the brake hose there to reduce the the stress. I used some heat shrink tubing to seal the joints and hold things together. The banjo bolts are just OE BMW (M10x1.0x18).



The CRF has a plastic brake line guide that mounts close to the center of the lower triple clamp. It was not possible to use this with the Trail Tech Race Lamp so I made up a guide from aluminum that mounts to the fork upper with a large hose clamp. For a trim look I used a European spec clamp that has the thinner band width.



Here's how the guide mounts to the fork. I made the hole big enough to slide a hose end through, but since there's no split in the guide I'll need to remove a hose end from either the master cylinder or the caliper to get the guide off the line.



After getting the line on and the system bled I found that two of the caliper pistons were sticky, so I took the caliper apart to clean it up and found some build up on those pistons. The seals didn't show any wear so I didn't replace them.

This caliper uses internal dust seals, as apposed to the external seal of the OE R100GS caliper. I think this internal seal design would be effected by dirt riding more than the external seal design.



This photo shows the seal grooves of the caliper body. The inner groves are for the pressure seals, and the outer for the dust seals.



After the cleanup the caliper worked better. Heres a view of the lower line routing.



-x3300

*x3300, Sep 24, 2010:*

I saw this R100RT monolever arm up for sale so I figured I'd see what could be done with it.





Here are a few shots that compare the parlever arm to the monolever.







The GS wheel fitted to the monolever arm. There's about a 20 mm gap betwen the hub and the final drive.





I did some measurements to get an idea of wheel travel limits with the monolever arm. In both the topped-out and bottomed-out case the limiting factor was the u-joint rubbing on the inside of the swingarm.







To get the drive shaft out of the swingarm I made up this spring compressor. The threaded parts extra long so it will work with longer swingarms.



Here's the compressor in action.



The u-joint was going bad so I'll need to replace it. I pressed the bearing caps out with this press, but I think just the screw of a bench vise would give enough force.



Once the bearing cap was pressed out as much as it could be I grabbed the end of it with a bench vise and hammered the yoke off it.



The disassembled arm and shaft.



I did this mock-up to see where things could go.



-x3300

*fishkens, Sep 24, 2010:*

Neato. Looking forward to the next update.

Thanks.

*rediRrakaD, Sep 25, 2010:*

X303,

Heading in this direction???



*x3300, Oct 1, 2010:*

rediRrakaD, whether or not we have realized it yet, I think we are all heading there.

I took a trip over to the scrap yard to look around for some stock I'll need while working on the monolever arm.

Here's what I found from the left; two 3/4" hardened bolts for the shaft, one of which I hoped would work, a section of 2"x1/16" tube for a cross brace, a rusty piece of 1" square tube for a fixture brace, and a section of 3"x2"x3/16" rectangular tube to make up the main part of the fixture.



My idea was to have a T-shaped fixture made of heavy gauge rectangular tube that would clamp the front of the swingarm at the swingarm pivot bearings, and then to have an indexable end plate that duplicates the final drive mounting pattern to hold the rear of the arm. The indexing of the end plate would allow it to hold swingarms of differing lengths.

I made up these swingarm fixture drawings to work with:

  bearing plug drawing  http://stuff.gotdns.org/bike/orgs-build-up/28-swingarm-fixture/bearing-plug.dxf
  angle plate drawing   http://stuff.gotdns.org/bike/orgs-build-up/28-swingarm-fixture/angle-plate.dxf
  main arm drawing      http://stuff.gotdns.org/bike/orgs-build-up/28-swingarm-fixture/main-arm.dxf

The main arm acts as a stable base for the other parts and allows indexing of the angle plate at 25mm increments. Arms of 0, 50, 75, 100, and 125mm. I don't think 25mm worth the effort, and the two index holes at 50mm were actually an error in my drawing that I didn't catch until after I got the machining done.



The angle plate duplicates the mounting pattern of the final drive and holds the rear of the swingarm in position. The lower section of the plate has two 10mm chromed pins pressed in that allow precision positioning of the plate on the main arm. The pins provide the alignment, and two 13mm bolts provide the attachment force.



The bearing plugs fit into the bores of the swingarm pivot bearings and clamp the front of the swingarm in position. Two bolts with 15mm of the diameter turned down fit into the center hole of the plugs. These bolts then thread into nuts welded on the front risers of the fixture.



I found these concrete anchor bolts are a handy way to pull the swingarm bearing out of the race.



I decided to make the angle plate out of aluminum because aluminum is easy to work with, but I think now it would be better made of steel since it seems as it will wear fast. I bored out the big hole in the angle plate and drilled the holes with this setup.



Here's a detail of the main arm and angle plate. This gives a good view of the angle plate's alignment pins. The bolts fix the plate to the arm and are 1/2-20 UNF grade 8. The hole in the far end of the arm is to accept a bolt that will act as a jack screw to keeps the swingarm from rotating on the front bearing plugs. I found I needed to reposition this hole outward as seen in other photos.



Anyway, after a while I had this collection of fixture parts assembled and ready for welding.



To get the arms aligned for welding I clamped them down to this piece of 3/8" aluminum plate.



I welded nuts onto the fixture at the bearing plugs and the jack screw. After welding I needed to chase the threads. This photo also shows the jack screw bolt and how I put a rounded profile on the top to get a constant contact area between the bolt and the swingarm when the bolt is turned.



And the finished fixture, its relly a heavy beast.



Here's another view with the arm installed. The idea for use is to set the angle plate at the 0 index, bolt an unmodified arm to the angle plate, then close up the bearing plugs, jack screw and top clamp such that the arm is held in place without any bending force, then cut the arm with a hacksaw and move the index plate to a new position.



After having the actual fixture and with some fitting of the arm to it I think the bearing plug method of holding the arm will be difficult to control accurately. I think it will be enough with some careful setup, but I think something with fixed alignment stops welded to the fixture may work better.

-x3300

*fishkens, Oct 1, 2010:*

Fancy! Keep up the great work.

*x3300, Oct 8, 2010:*

I did some hunting around the Internet and took a few trips to local MC dealers with a tape measure in my pocket to collect some info on rear suspensions. I'm not sure of how wheelbase is measured, but I put down what I measured with the bike supported and the suspension topped out, plus an adjustment for the longer swingarm. Here's the tally; wheelbase, travel front and rear, swingarm length, final drive ratio:

  bike     wbase front rear salen final

  R80G/S   1465  200   170  410   3.36
  CRF250R  1478  315   315  ?     -
  R100GS   1514  225   180  455   3.09
  R1200GS  1520  190   200  533   -
  F800GS   1577  230   215  622   -
  HP2      1610  270   250  575   -
  HPN-Adv  1620  295   240  510   -
  ORGS     1622  280   280  535   2.91

It seems 100mm is a common monolever swingarm extension. I wanted to get some more travel and figured I'd try 125mm, so 80mm more than the max of the R100GS paralever swingarm.

I marked the cut with a Sharpie pen, put the arm in the fixture, then went at it with a hacksaw. I put the cut where the swingarm tube runs exactly parallel to the centerline of the bike so that both swingarm tube and the extension tube ends would need 90 degree cuts.



Here's a view of the section.



The 2"x1/16" tube I mentioned in the previous post was intended for the cross brace. I bolted the back end of the arm at the 125mm index of the fixture then measured the angles the cross brace would need. I set the brace to give the maximum support and have just enough clearance to fit an 18" wheel.

I used this hole saw and a vertical mill to cut the tube ends. I set the head at the needed angle then made the cut.



The hole saw wasn't long enough to cut straight through the tube, so I needed to cut until the saw bottomed, remove the tube from the vise and cut off the scrap, and then remount the tube and continue with the cut.



I drilled this small hole in the bottom of the brace to vent the tube while welding.



Here's the arm and additions cleaned up and ready for welding.



I used masking tape to hold the extension in place for tack welding. I cut out small sections of tape and made the tack welds.



I used this big C-clamp to hold the brace in position for tacking.



There wasn't much room between the bottom of the arm and the fixture so I needed to use this short tungsten cap to get in there.



Welding in progress.



And the finished arm out of the fixture.



I measured the arm before and after welding with this height gage to check the alignment.



Here's the arm installed with a fender and shock mock-up.



I really like the look of the triangle the arm and big cross brace make just in front of the wheel.



I'll need to look into and decide on a shock before setting up the shock mounts.

-x3300

*fishkens, Oct 8, 2010:*

x3300 said:

I marked the cut with a Sharpie pen, put the arm in the fixture, then went at it with a hacksaw. I put the cut where the swingarm tube runs exactly parallel to the centerline of the bike so that both swingarm tube and the extension tube ends would need 90 degree cuts.

-x3300 Click to expand...

Still my favorite thread.

But a hacksaw? Is that because you don't have a cutoff saw or band saw where you could set a jig to cut at a 90 degree angle or because you felt you could cut an equally square cut in the same time with a hacksaw or for some other reason. Just curious.

Thanks.

*x3300, Oct 9, 2010:*

fishkens said:

But a hacksaw? Click to expand...

Hi fishkens,

I used a hacksaw because I wanted to make a cut that was relatively narrow and also precise. I didn't want to have a big gap to weld up, nor to mess around with grinding and fitting the pieces. I think it would be difficult to get that fixture into a bandsaw at the correct orientation. With the arm cut accurately I could just cut the extension tube to 125mm (on a horizontal bandsaw) and weld it in.

The swingarm tube is thin and made of mild steel, so easy enough to cut by hand with a sharp blade. I made an accurate mark around the circumference of the tube with the marker and just made sure the cut was always progressing along that mark.

-x3300

*NOTICES*

All ORGS design materials are relesed under the Fabricators Design License.

Copyright x3300

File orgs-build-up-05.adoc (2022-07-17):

:url-bmw-frame-gussets: https://www.advrider.com/f/threads/bmw-frame-gussets.638795/
:url-frame-gussets-svg: https://github.com/moto-design/bmw-frame-gussets

:imagesdir: images

:notitle:
:nofooter:

= ORGS Build Up - Page 5

[big]*The ORGS Build Up Project*

*Page 5*

*fishkens, Oct 9, 2010:*

I knew you had considered the options so thanks for the explanation.

Keep up the good work.

*rediRrakaD, Oct 10, 2010:*

X3300 (got it right this time),

I think the 100mm extension idea stems from the folks @ HPN.

I'm currently working with Phil @ Aftershocks (Palo Alto) on the proper shock for my rig (Wilbers custom). He may be able to add some insight to your project as well... smart guy, when it comes to suspension/geometry.

Really enjoying your thread. Thanks for taking the time to post. Cheers, S.

*Beater, Oct 14, 2010:*

Holy Crap. This is the first I've read this ...

I have an '83 r80 looking for just this kind of treatment.

Sub-freakin-scribed.

*x3300, Oct 15, 2010:*

The long swingarm will need an extended drive shaft to match.

As a start I measured the stock shaft to get a kind of baseline. I used this height gage and a ground pin to measure the length. I zeroed the gage with the pin under it, then put the pin in the yoke bores and took the reading at the top of the pin as the length of the shaft to the bores. It measured 284.27mm.





The stock shaft is center drilled on both ends, so I put the shaft on a lathe between two centers and setup a dial indicator to check the runout at the center of the shaft. I measured .064mm max.



My plan for the extension was to cut the shaft at its center, drill a 5mm hole in the end of each of the resulting sections, then make an insert that had a section on each end turned down to 5mm. The turned down sections would press into the holes to hold the insert in alignment for welding.

Here's the machining of one end of the insert. I turned the end down to 5.1mm, and on this end I put a very small center hole to use when aligning the first weld joint.



After I got the shaft and insert ready I pressed the insert into the shaft with this arbor press. The shaft plus insert was too long to fit into the press so I used these C-clamps and a piece of steel plate to make a base to press against.



After I got the insert and one shaft section pressed together I mounted them in the lathe and checked the runout. To adjust the alignment I supported the shaft with blocks on each end and tapped on it with a plastic mallet. After a few iterations of checking and tapping then checking I could get the runout to about .015mm.



With the insert aligned I tack welded the joint then put a bead all the way around the shaft.



I let the shaft cool slowly and then ground away the excess bead.

The stock shaft was heat treated, but I decided it would be better to leave the shaft soft at the weld points than to try a heat treatment and have it too brittle. If I have trouble with it when I put it into use I'll consider having it done by a heat treating service. After welding I found the runout was close to 1mm.

I used this setup to get the shaft aligned. It took a few trips between the lathe and press to get the shaft back to about .060mm runout.



After the first joint was finished I repeated the process on the second joint. Here's the shaft just after finishing the second bead.



After the insert was fully welded in I did a final alignment of both weld joints to get the final shaft runout to about .060mm.



With the shaft aligned I could then turn down the weld beads to the diameter of the shaft. I mounted the shaft in this four-jaw chuck and used a dial indicator to get it precisely centered for machining.



I saw a monolever arm and shaft up for a reasonable price, so figured it wouldn't be a bad idea to have a spare on hand. Here's how the extended parts compare.



After finishing the extension work, I can say that I don't think my method of a press fit alignment was a good one. I think a better way would be to make a fixture that holds the shaft ends and the insert in position for welding.

Here's a shaft fixture drawing of what I'm thinking about. It can handle +100mm and +125mm shafts. I have some 3"x2"x3/16" rectangular tube left over from the swingarm fixture I can use for the base and I'm thinking I'll pickup some rectangular bar stock for the V-blocks next time I'm at the scrap yard.



-x3300

*fishkens, Oct 15, 2010:*

x3300 said:

After finishing the extension work, I can say that I don't think my method of a press fit alignment was a good one. -x3300 Click to expand...

Why don't you think the press fit was good? I was going to ask why you didn't drill both the shaft ends and the insert ends and use dowels (v. turning down the ends of the insert) but it sounds like you'd perfer a butt joint welded in a jig.

Any clues are welcomed.

Lovin' your work.

*Caddy82rats, Oct 16, 2010:*

your work is incredible, thanks for sharing this art

*Airhead Wrangler, Oct 16, 2010:*

x3300 said:

I think a better way would be to make a fixture that holds the shaft ends and the insert in position for welding. Click to expand...

Inertial friction welding is the way to go for solid driveshafts. It welds the whole cross section. I'm guessing you probably aren't set up for that though. You might be able to make it work on your lathe though.

https://youtu.be/I8QJQ4lvybQ

*Stagehand, Oct 16, 2010:*

I always wondered if it was better to just use two shafts, and only make one splice. You know, cut each one off center, and use the longer of the two sections.

*Stagehand, Oct 16, 2010:*

Airhead Wrangler said:

Inertial friction welding is the way to go for solid driveshafts. It welds the whole cross section. I'm guessing you probably aren't set up for that though. You might be able to make it work on your lathe though.

https://youtu.be/I8QJQ4lvybQ

wow that is pretty cool-

and yeah, agreed, this is great work. Fun to watch, too.

*fishkens, Oct 16, 2010:*

Airhead Wrangler said:

Inertial friction welding is the way to go for solid driveshafts. It welds the whole cross section. I'm guessing you probably aren't set up for that though. You might be able to make it work on your lathe though. Click to expand...

Wow. Simple as that.

Thanks.

*DRjoe, Oct 16, 2010:*

I've welded solid drive shafts together on outboard motors before by cutting both ends at an angle (about 60), clamp both pieces in a bit of angle to align them and then weld.

but my so called engineering is a bit rough so best not to do what i do

I've also seen crankshafts extended by putting a matching taper on both pieces then pressed together and welded. I like this way because in theory the taper should take the load.

*Zebedee, Oct 17, 2010:*

Fantastic stuff

Many thanks for the continued updates

John

*x3300, Nov 5, 2010:*

I've been down riding the black and yellow R100GS in the Mexican Sierra Madre mountains for the past two weeks so haven't been able to make any progress on the build-up.

I did about 1000 miles (1600 km) of dirt riding that really gave me the experiences and the time to think again about the limitations of the R100GS and what I want in my ORGS. Here's a clip from an easy section that shows what I want this bike for.

https://youtu.be/2WIEh48R6r0

fishkens, it is much easier to make a pin accurately fit a hole than it is to make a hole accurately fit a pin, and that is why I didn't use a standard dowel pin, but even drilling the holes and turning the insert ends down to fit was too involved. Also, the void in the holes not taken up by the insert ends can trap air and machining oil which can expand and cause weld contamination and/or weld inclusions. I think holding the parts externally with a v-block fixture is easy and is as accurate as holding them with an internal pin, and the entire cross section can be welded with a butt weld setup.

Airhead Wrangler, friction welding takes a lot of force and a lot of power, it needs some specialized equipment to get the pieces melted then to hold them together until they solidify. Just for anyone interested, check out friction stir welding, a similar technology.

DRjoe, my welder has a pulsed DC feature that I can set a high pulse frequency to get a relatively narrow and deep penetration without having a big chamfer. I found a narrow notch at the joint seems to work OK, and with this method I don't need to add a lot of filler.

-x3300

*fishkens, Nov 5, 2010:*

x3300 said:

fishkens, it is much easier to make a pin accurately fit a hole than it is to make a hole accurately fit a pin, and that is why I didn't use a standard dowel pin, but even drilling the holes and turning the insert ends down to fit was too involved. Also, the void in the holes not taken up by the insert ends can trap air and machining oil which can expand and cause weld contamination and/or weld inclusions. I think holding the parts externally with a v-block fixture is easy and is as accurate as holding them with an internal pin, and the entire cross section can be welded with a butt weld setup. Click to expand...

Okay. I'm familiar with drilling a hole and then reaming it out to size to fit a standard dowel as opposed to machining the pin. But I barely know enough to be dangerous and understand how machining the pin could be easier.

Thanks.

Looking forward to more.

*Airhead Wrangler, Nov 6, 2010:*

x3300 said:

Airhead Wrangler, ... check out friction stir welding

Click to expand...

I like. Hadn't seen that one before.

*rediRrakaD, Nov 6, 2010:*

^ +1. S.

*petekeys, Nov 11, 2010:*

Hi Geoff

Now you are set up with jogs and everything, are you going to offer this as a service?

If so then how much would you charge?

cheers

-Pete

*petekeys, Nov 11, 2010:*

Stagehand said:

wow that is pretty cool-

and yeah, agreed, this is great work. Fun to watch, too. Click to expand...

Is it possible to do this in a conventional lathe? There must be a fair amount of pressure being applied between the two shaft so maybe its not doable in a lathe.

*x3300, Nov 13, 2010:*

petekeys, this project is about realizing my vision, about creating the machine and executing my plan, and also of course about telling the story. Once I create something I really have little interest in doing it again for someone else, unless maybe if it allows me to be involved in some cool project or enterprise. I don't want to get into a discussion about it, but if someone wants to do such a service, all the photos, drawings, and documents from the project are my own and I am the sole copyright holder, but I release them to the public under the terms of the Fabricators Design License. The spirit of the license is to allow anyone to use the material for whatever use they want as long as any modifications or improments to the original design are made available to the public at no cost.

As I mentioned in a previous post, the u-joint of the shaft I extended was going bad so I intended to replace it. I measured the OE joint as 19x44. Here's the joint in the original shaft.



After some searching I found two after market u-joints I thought might work. One is a 19x44 and the other a 19x48. From the left; the 19x44, the 19x48, and the OE joints.



I was interested in the 19x44 because there's not much clearance between the transmission output flange yoke and the swingarm housing when the swingarm is in the bottomed-out position with my 280mm of wheel travel. I thought with this joint there may be enough room to add a circlip to the yoke to hold the joint in place, but when I got the part I found it to be of very poor quality, and I think intended for steering shaft applications. As seen in the photo the bearing inner shaft has a very small diameter and the needle bearings are much shorter then the OE joint.

Here's a comparison of the OE joint on the left and the 19x48 on the right. The OE joint has larger diameter bearing shafts and longer needle bearings than the replacement 19x48. I think the OE joint would have longer service life in the monolever's splash lube application, but the 19x48 should be sufficient for my application. I am still on the lookout for a better replacement, ideally something near identical to the OE joint.



The bigger 19x48 didn't quite fit into the yokes.



I used a die grinder to take a small amount of material off the yokes and the joint cross.



Here are the shaft parts ready for assembly. The photo shows where I ground two ribs off the joint cross to get the needed clearance for assembly. The replacement joint has a grease fitting and shaft seals, but I didn't install these to allow the gear oil in the swingarm to get to the joint bearings.



The 1st step in assembly is to get the cross in the yokes.



Next is to install the caps. I used a brass hammer and some sockets to get caps in place. The photo shows how I used a socket large enough to pass the cap to support the yoke from below. Some light tapping was enough to get the caps positioned.



I used a depth micrometer to center the caps in the yoke such that there was no play in the joint bearings.



As mentioned, with my increased wheel travel there isn't much clearance between the transmission output flange yoke and the swingarm housing at the bottom-out limit, and with this bigger joint the options for fastening the joint were few. My 1st idea was to make a strap, maybe 5mm wide that would go across the cap and be spot welded to the yokes, but in the end I decided a simpler solution was just to spot weld the cap to the yoke.

I knew that it was somewhat common method, especially in off-road trucks, but wasn't sure if it would work here. To get a better feel for it I cut up a cap from an old joint with an abrasive cut-off tool to see the cross section.



I figured that if I did the welds with minimal penetration there was a lot of material there at the end to take the weld, and also, all the u-joints I've ever seen always wear out at the load bearing sides of the needle bearings, so if I put the weld somewhat perpendicular to that the effect of the weld would be minimized. I setup the welder with a low amperage and the DC pulser at around 5 Hz. I just put one weld at the thicker end of the yoke. I can try putting a second weld at the other side if I find trouble when I put it into use.



There wasn't much else to do other than weld the other caps on. Here's the finished shaft.



And the shaft installed on the bike. This shows the yoke clearance problem. When the shaft turns a few degrees from this position the corner of the yoke will almost touch the arm housing.



I have a spare joint, so when it comes time to replace this joint I'll just need to grind away the spot welds to get the caps out and put in the new joint.

-x3300

*Beemerguru, Nov 13, 2010:*

Great project and wonderful workmanship.

I'm just starting another G/S..this time going retro with a dual shock version of the original late '70s G/S. Of course the frame needs some bracing and wondered if you had any left over finished gussets or if the vector graphic data is still available?

Thanks

Greg in Foster City

*NOTICES*

All ORGS design materials are relesed under the Fabricators Design License.

Copyright x3300

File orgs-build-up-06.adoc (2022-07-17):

:url-bmw-frame-gussets: https://www.advrider.com/f/threads/bmw-frame-gussets.638795/
:url-frame-gussets-svg: https://github.com/moto-design/bmw-frame-gussets

:imagesdir: images

:notitle:
:nofooter:

= ORGS Build Up - Page 6

[big]*The ORGS Build Up Project*

*Page 6*

*maverick, Nov 14, 2010:*

Just another WOW and thanks for sharing the info. Simple question is the swingarm extention tool you welded up just based on a 90 degree angle when it extends out to the longer sections or at a slightly different angle as the shaft is not entirely centre to start with on the original swingarm if that makes any sense?

*x3300, Nov 20, 2010:*

maverick, I assume everything is aligned; trans output shaft, final drive input shaft, swingarm pivot, etc. I didn't check that, but I can see my extended shaft and arm seem to have the proper alignment.

Beemerguru and others, I have received a lot of inquiries about the gussets so I created a new thread dedicated to them here: [thread]638795[/thread]

To get the rear wheel travel I wanted with my extended swingarm I either needed to fit a custom shock to work with the original GS upper shock mount or make a new shock mount to fit a shock from some other bike.

Modern off-road suspensions have progressive damping, where the damping increases as the shock compresses. This is done either through a linkage mechanism or through shock valving. Such systems have been well received, so I figured I'd try to get some progressiveness in my design. Since the GS has no linkage I would need to fit a shock with progressive damping. Not too many bikes use such a shock and this requirement would really limit the shocks I could choose from.

As a start to get an idea of what shock length and stroke values would work for my application I made a spreadsheet that calculated the shock length and stroke needed to get my 280 mm of travel using the original GS upper shock mount. I set it up to do the geometric calculations at 2 mm increments along the swingarm.



I used the values to compare what would work with what was available from various shock catalogs. I wasn't so lucky, no stock shock would work with the original GS mount, and the only progressive shocks that seemed like they might work were from a BMW G 450X, or a few of the KTMs. I figured KTMs are pretty common compared to a BMW G 450X, so decided on fitting a KTM shock. After a bit of searching around the Internet this box arrived with an Ohlins TTX44 for a KTM 250 SX-F. The length is advertised as 410.5 mm and stroke 109 mm.



With the shock in hand I could estimate how much the stroke was decreased by the bottoming bumper and how much space was needed between the lower shock mount and the swing arm centerline. Both these need to be considered in the design.

The geometric equations that describe the set of mounting points that would work with this shock are non-linear and difficult to solve for even using numeric methods, so I decided to use a graphical method. I used a large piece of paper to layout a full scale drawing with the swingarm pivot, upper shock mount, and swingarm at the upper and lower limits of travel. I used two thick pieces of paper marked at the extended and compressed lengths of 410.5 and 306.5 (5.0 mm bumper thickness) to find a set of mount points that would work.



Here's the detail near the top mount. As the drawing shows, any lower mount from about 240 mm to 320 mm rear of the swingarm pivot won't work with this shock because the frame tube is in the way of the top mount. The points from around 320 mm on back could give the proper wheel travel but would put the upper mount in the middle of the frame tube and I thought that that would put a lot of bending load on the tube so I chose not to use those points. Around 230 mm seemed good. This would put the shock and mount up above the original shock mount, but I thought it would be OK since I needed to make a custom sub-frame and seat anyway.



Once I got some mount points I thought would work I laid those out on the frame and swingarm with some masking tape to do an initial check of the fitting.



When I was confident I didn't need the upper mount I used a cutoff wheel and angle grinder to remove it, then laid out some mount points on card stock tapped to the frame.



And checked what would give enough clearance between shock and frame.



To accurately check the fitting with the swingarm in the up and down positions I made this jig with holes drilled at 410.5 mm and 306.5 mm.





Then, after all the checking I made this paper template for the upper mount.





Here are the upper and lower mounts I made up. I thought it would be hard to do the bends a one piece upper mount would need so I decided to make it from two pieces that would weld together.



First I welded on the outer piece.



And then the inner.



Here's a view from the inside with the shock in place.



With the upper mount welded on I used the jig to mark arcs at the extremes of swingarm angle at my chosen lower mount point (230 mm from the swingarm pivot). The red shows the upper limit that would not allow the transmission yoke to contact the swingarm housing when the suspension bottomed out, and the green the lower limit that would keep the transmission output flange bolts from tearing up the rubber swingarm boot when the suspension topped out. I would have liked a little more margin for safety, but had to accept what I was faced with. The black cross shows my drill point.



The lower mount would need a spherical rod end bearing to match the shock's lower clevis mount. Some searching in the McMaster-Carr catalog showed two bearings that could work, a 12x30x16 metric bearing and a 1/2"x1"x1/2" inch bearing. I decided on the 1/2"x1" bearing since it was cheaper and would allow a lower profile mount. I made up this mount from some rectangular tubing and round stock.



Here are the internal parts of the lower mount. I bored out the round stock to allow a press fit of the bearing and turned down the edges of some aluminum stock to make two spacers that allow the joint's ball to rotate a few degrees.



Here are the pieces assembled and the joint set at its limit.



And the mount tack welded to swingarm. The shock is installed for checking. I'm thinking to make some short tube shaped seals from neoprene sheet to keep dirt and water out of the bearing.



Not much was left to do other than to finish the lower mount welds. Here's a view from the rear of the finished installation. The reservoir at 45 degrees sticks out a little, but I'll make the sub-frame go around this as needed.



And a view from the side.



I'm really happy with the result. 280 mm (11") of travel and a first class shock. The hollow lower mount gussets didn't work out as well as I thought they would. The rectangle tube wall was relatively thin and difficult to weld to the thicker swingarm. I think some gussets from 1/16" or a little thicker sheet, maybe with some drilled holes would be better.

-x3300

*Mr. Vintage, Nov 21, 2010:*

Awesome, as usual.

*x3300, Nov 26, 2010:*

The R100GS takes a huge battery, so I figured I could save some weight and make more room for a bigger tool tray if I fitted a smaller one, with the expectation that I would replace it more often to keep it up to peak capacity.

I looked through the Yuasa battery catalog and found the YTX14AHL-BS which seemed like it might be enough. Its used on some other big displacement bikes. Here's how the specs compare to the 53030:

  model       AH CCA acid   weight L   W   H
  53030       30 ?   1600ml 7.3kg  186 130 171
  YTX14AHL-BS 14 210 660ml  4.1kg  134 89  166

With a little searching I found one advertised cheap locally so picked it up to try it out. Here's how it compares to the original GS battery.



To start I made up a paper model to find the best fit in the frame and get an idea of styling that would look good.



Here's a slightly revised version of the battery tray drawing for the unfolded sheet metal. As seen in the photos following my original design didn't have the full front panel this drawing has.



I used some 16 gage aluminum sheet I had that was left over from the dash, and after a quick layout with a Sharpie marker I used this holesaw and drill press to make the big side holes. These holes were bigger in my original design, and I found they removed too much material which left the sides a bit too flimsy.



I could make the smaller holes with this rotex sheet metal punch.



Here's the plate with the main holes. I don't have a photo of it, but next I punched four very small holes at the intersection of the fold lines then used a corner notcher to cut out the corners. The holes help to make a smooth bend.



I used a sheet metal brake to bend the panels up. Also shown are the mounts I cut from aluminum angle. To be safe I made the mounts a bit longer than I measured was needed with the intension of trimming them down after welding and fitting.



Here's the finished tray with the corners and mounts welded, and mount holes drilled.



The old and new parts compared.



Here's how the tray fits in the frame. It leaves a lot of room for a big tool tray, exhaust pipes, and muffler. I still need to clean up the mount ends and add a hold down strap.



And a view with the battery. This photo doesn't really show it, but the contrast between the dark battery and the shiny aluminum makes the strip and five holes look really good.



As mentioned, this first version is a little flimsy, I think the new version of the drawing will be enough in 16 gage aluminum, maybe with a slightly stronger attachment of the mounts to the tray panels.

-x3300

*x3300, Dec 5, 2010:*

I'll need some kind of spring to hold up the back of the bike. As I mentioned in an earlier post modern off-road bikes have progressive suspension systems where the damping force and spring rate increase as the shock compresses. Most bikes use a linkage mechanism to achieve this, but some have a linkless design where the progressive effect is accomplished with progressive shock valving and progressive rate springs.

Here's a nice spring force diagram from Race Tech:



With some searching I found two progressive springs on the market that I thought would fit my TTX44 shock. One is the Race Tech 6326 Series.



The other is the Langston Racing Super Progressive.



Just based on these two photos the Langston spring seems to have a much more progressive wind than the Race Tech.

Here's a comparison of the recommended springs for a 250 SX-F from Ohlins, Race Tech and Langston. The stock spring rate for the 250 SX-F is 62 N/mm.

  rider weight  Ohlins     Race Tech  Langston
  kg (lb)       N/mm (lb/in)          N/mm
  64 (140)      -          6326P05    -
  69 (152)      -          -          LRS-01 64-132
  70 (154)      60 (343)   -          -
  75 (165)*     62 (354)   -          -
  76 (167)      -          6326P10
  80 (176)      64 (365)   -          -
  85 (187)      66 (377)   -          -
  90 (198)      68 (388)   6326P15
  95 (209)      70 (400)   -          -
  105 (230)     -          6326P20    -
  109 (240)     -          -          LRS-02 83-176
  120 (265)     -          6326P25    -
  136 (300)     -          6326P30    -

To get a handle on which of these would work with my custom rear suspension I considered how the ORGS rear compares with some linkless KTMs.

  bike          style  travel(mm) ratio weight(kg) rate(N/mm)[/b]
  KTM 250 SX-F  MX     335        3.07  100        62
  KTM 450 SX-F  MX     335        3.07  105        68
  ORGS          trail  280        2.57  200        -

This bike will be much heavier than a 250cc MX bike, but it will mainly be used on trails, and the shock leverage is about 80% of the KTMs. I thought I'd rather have the back end a little too soft than too stiff, so I decided on the Race Tech 6326P10. The LRS-01 was another choice, but I thought it might be too stiff near bottoming. I put in an order and this arrived.



Here's what I measured it to be:

  Race Tech 6326P10
  length = 260mm  10.35"
  ID     = 63mm   2.48"
  wire   = 13.0mm 0.51"

Pretty close to 2.5" x 10", a common size of off-road racing truck coil-over springs. I've never seen any progressively wound truck springs though.

To get the spring on the shock I needed to make a spring compressor. Here's an updated version of my ohlins spring plate drawing.



The design is similar to my drive shaft spring compressor. A base plate has two arms welded to it.



And two bolts are welded to the arms that pass through the plate.



Here's the unit in action. I made the arms long enough to allow a block of plastic at the bottom to keep the shock from getting scratched.



This photo shows how the 36.5mm radius cut-out allows the spring clip to be placed in position while the spring is compressed.



And the shock with spring installed. I noticed that the spring hits the corner of the battery. I thought that it might after I got the new tray done. There's enough room to move the battery to the left a little. I just need to drill another set of mounting holes in the tray.



With the shock installed I checked the free sag and ride height. For the 250 SX-F Ohlins recommends 30mm and 110-115mm for those. Converting by 109/335 gives 9.7mm and 35.8-37.4mm at the shock shaft. I measured 10mm and 28mm, which would seem a little too stiff, but I think it will be OK with the heavy bike, and the next lighter spring in the 6326 series is considerably lighter. After I get some trail riding time on the bike I'll be able to judge how well this spring works. I guess I'll need a stiffer spring while carrying traveling gear.

I spent a lot of time researching springs, studying the data, and writing up the report, but the rear suspension is a big part of what this bike is and so I wanted to give selection of the spring proper coverage.

-x3300

*fishkens, Dec 5, 2010:*

Thanks for the detailed posts. I learn something every time I visit your thread.

*Zebedee, Dec 5, 2010:*

fishkens said:

Thanks for the detailed posts. I learn something every time I visit your thread. Click to expand...

I'll second that ...

Keep up the good work.

John

*brunocrossley, Dec 16, 2010:*

X3300, please tell me. Are the upper and lower shock mounts exactly perpendicular to the swinging arm pivot axis, or do you allow for any misalignment with the rose joints? I'm trying to do something similar with a 'twin shock-to -mono' arrangement and find that the available target area on the main frame loop is inboard of that on the swinging arm. The shock wants to point in towards the spine of the main frame, and is trying to twist the conventional rubber shock-mounting eyes. I suppose that rod-ends would allow for that?

I know it would be easier to find a mono frame, but where's the fun in that?

Mark

*x3300, Dec 17, 2010:*

brunocrossley said:

The shock wants to point in towards the spine of the main frame, and is trying to twist the conventional rubber shock-mounting eyes. Click to expand...

brunocrossley, It sounds to me like you need to remove the old mounts and make some new ones where they will be aligned.

I setup up the shock mounts so that the center of the shock end bearings were in the same plane, and that that plane was perpendicular to the swing arm pivot when the swingarm was centered in the swingarm bearing adjustments. With the lower clevis mount I can make adjustments with a thicker bearing spacer on one side if the swingarm needed to be moved over for drive shaft clearance or whatever, but I don't think that will be needed.

This photo shows the mounts from the rear.



-x3300

*x3300, Dec 18, 2010:*

With the extended swingarm and KTM shock there's no way the OE subframe will fit, and the subframe is something I thought I could replace with a lighter and simpler design.

There were a lot of things I needed to consider for the subframe design. It needs to support the seat, rear fender, tail light, license plate, luggage racks, muffler, etc., in such a way that they all fit and work together, plus it also needs to clear the tire when the suspension bottoms out and somehow needs to connect to the main frame and be strong enough to hold the rider and luggage. With just blank nothingness at the back of the bike the task seemed a little daunting at first. Here's what I was faced with:



To get an idea of what would work I made this mock-up with some aluminum flats I happened to have. I wanted to have as much as possible just straight tube so it would be easy to build and so it would have good load bearing for the weight.





Once I had an idea of what would work I made up this subframe drawing to work with. The GS subframe is made of 18mm thick wall tube. My idea was to make a lighter weight unit of 3/4" (19mm) thin wall 1018 steel that may not be as strong, but had a simple design that could be easily replaced when damaged or updated with a chromoly or aluminum version without much effort. The design has only two bent tubes, the right front support needed to bend out to clear the shock reservoir, and the rear connecting tube needed to loop up and around the fender.



To prepare the tube ends for welding I used a 3/4" end mill on a vertical milling machine to plunge into the tubes at the proper angels. I didn't have a 3/4" hole saw but the end mill worked OK. The other cuts I could do in a standard milling vice but for the shallow cut on the lower front supports I needed to use this angle plate setup. It wasn't a very solid setup so I used a 4 fluted mill and went in real slow. I've since bought a 3/4" ball end mill that will allow me to do shallow angle cuts in a vise.



I have access to a Hossfeld tube bender. It only has press bending dies, but I thought that it would be enough to do the front support tube. I'll make up a set of 1/2" rotary draw dies to do the rear connecting loop and a top luggage rack. This photo is just a setup I did later to show the bender. When I did the bend I filled the tube with sand and sealed the ends with PVC electrical tape. The sand supports the tube from the inside and gives a smother bend.



With the tube ends done and the front support bent I did a trial fitting to check the tire clearance and figure out what kind of mounts were needed on the frame.



Here are the frame mounts I added. To get a shape and location that would work with my subframe I started with some templates from thick paper card stock then when I was satisfied with them I made up a set from 1/8" steel plate.



To add some strength at the mount points I put on a set of lugs made from 7/8" thin wall tube slid over the 3/4". The welded subframe would be too big to fit into the sandblaster I have access to, so I sand blasted the individual tubes in preparation for painting.



Here's a detail of a lug. I slid the outer tube over the main tube then crimped the end in an arbor press. I used a large open end wrench to form a rounded crimp edge which I thought would give a stiffer side-to-side crimp. I couldn't get enough force out of the press to completely flatten the tube and lug so I finished the crimp with a hammer and anvil. To finish the lugs I ground the crimped area to have a nice profile and have some clearance for the upper mounts, then welded a bead along the tube ends. In retrospect, I would have liked to put some relief on the ends of the lug to reduce the stress at that junction, similar to the way old lugged bicycle frames were done.



With the tubes prepared I did another trial fitting to check the tire, fender, and shock clearance. When I setup the shock I put it as far inboard as possible so that there would be enough clearance to allow a straight lower subframe support as seen here.



I used this carpenter's level to get the top tubes parallel to the main frame just before tack welding.



Here are the sides welded up. This photo shows the simplicity of the design.



To add some strength to the joining of the support tubes I made up this set of gussets.



I used this hole punch to punch the hole and cut out the reliefs.



And here's the subframe all welded up. I added a small plate on the middle cross tube to mount the fender.



And the subframe with a UFO enduro fender. I still haven't decided on a rear fender yet...



Here's a detail of the fender mount.



And a shot with my old seat pan, which unfortunately, will no longer work. I'll need to make a new one.



To finish the subframe I still need to make up the rear fender mount loop. I also plan to make a small detachable top luggage rack and two light weight detachable side luggage racks. All of these though depend on the rotary dies which need to be made.

-x3300

*Zebedee, Dec 19, 2010:*

Thanks for the detailed updates ...

Keep up the good work.

John

*fishkens, Dec 19, 2010:*

Love it.

I'm looking forward to how the luggage racks will be integrated. Do you think they'll bolt on or will they be welded for a permanent installation? Bolt on would be nice to allow removal and lighten the bike a up a bit when luggage isn't needed.

*turnipbmw, Jan 1, 2011:*

Love this kind of report !

if you need any more parts from the UK, I will be visiting my uncle in Cupertino in the spring so may be able to bring them for you

*datchew, Jan 1, 2011:*

Fantastic.

I eat this type of design and fab up! Yummy. :dg

*x3300, Jan 1, 2011:*

I've been down riding in Baja for the last week, so haven't made any progress on the build-up.

Here's a video from along the coast south of San Felipe where they run the Baja 250 race:

https://youtu.be/vWLamvA86ig

-x3300

*x3300, Jan 9, 2011:*

There are some differences between the monolever and GS paralever final drives. The brake drum and output flange diameters are the same, but the GS output flange is a lot shorter.



Here's how it looks when I mounted the GS wheel on the monolever drive. It can't be seen, but the brake shoes are hanging out into the gap. I figured it'd be best to try to fill up the gap somehow.



I planned to rebuild the wheel so I pulled out the hub to work on it.



Here's how it mounts up. I measured the gap as 22.5mm.



The hub has a center section that extends out. To cut it down I mounted the hub on a lathe with a four-jaw chuck and used this indicator to get the hub centered.



Then used this indicator and a mallet to set the axial alignment.



After a few iterations of radial and axial alignment I could get the hub set. I cut off 21.5mm to leave a 1mm gap between the hub and final drive.



After I got the center section cut down I checked for interference by pushing the drive into the hub and and turning it around.



I found I needed to re-shape the uncut center section to make room for the brake springs as seen here. The outer edge of the monolever drum seals with two ridges, but the spoked paralever drum has only one outer ridge with the spoke nipples directly below. I trimmed a little off the outer edge of the hub to make some room, but there wasn't enough material there to cut off, and have some regrets now since it didn't solve the problem.



To get the clearance I mounted the drive on the table of a vertical mill using this setup and cut 2mm off the inner sealing ridge. I just used the X and Y hand wheels while watching the cut to manually feed the cutter around the circular path.



Even with all the cutting I still found the brake spring damper caused the spring to rub on the hub. The damper is really thick and causes the spring to bulge out. I'm not sure if it will rub when the brakes are properly adjusted, since the spring will move out a little when the brake is applied. I'll try a thinner damper if the spring rubs when the brake is setup.



-x3300

*Rucksta, Jan 9, 2011:*

There is an alternate spring damper that is internal to the spring and does not incrrease the diameter

*x3300, Jan 23, 2011:*

Machining 21.5mm off the center of the rear wheel hub moved the hub that much closer to the swingarm. To fit a wide tire like the Gripster or TKC-80 I would need to offset the rim to the left to get the needed tire clearance.

With a stock wheel and Metzler ME 880 140/80 tire mounted I measured the gap between the swingarm and tire to be about 10.5mm. I also measured the Gripster to be about 4mm wider than the ME 880, so as a rough figure I thought I'd need about 14mm of offset to have a 3mm tire to swingarm gap. I didn't think I could move the rim over that much and have proper spoke/nipple engagement with stock length spokes. I did have a set of stock length spokes I had bought to use with the paralever rear end, so I decided to do a temporary wheel build with them to get the length difference needed to have proper engagement.

The spoke holes in the hub and wheel are drilled so they are close to being aligned when the wheel is assembled. With a rim offset of 14mm the holes would no longer be aligned. I decided to re-angle the holes a little to reduce the bend of the spokes. Due to the geometry of the wheel some spokes needed a little more rework than others. At first I used a hand drill with a twist drill to do the rim, but then switched to a small end mill chucked in the hand drill which gave me better control.



I used an appropriately sized twist drill to do the hub.



During my first attempt at building the wheel I found the spokes on the right hand side started to protrude into the nipple so much that the allen key would no longer engage. To continue I ground 3mm off the threaded end of half the spokes. I used this caliper as a length gage while grinding.



The rear wheel lacks the bearings of the front wheel, so poses a challenge on how to support it for truing. I used the final drive and swingarm held up in a vise. I found that with no oil and the drive shaft splines disengaged it wasn't too bad. I needed to take the wheel off the drive to work on the spokes that had nipples inside the hub though. I didn't need super precision for the run-out, so I just used this setup with a sheet metal pointer held with a c-clamp.



Once I got the wheel built I checked the tire clearance with several different tires mounted, and it seemed the 14mm offset would be OK. I used this 3mm screw and nuts as a depth gage and found I needed the left hand side spokes 6mm longer. The spokes had enough of the length threaded so that I would be able to use the shortened ones on the right hand side.



Here's the wheel with a TKC-80 tire mounted that shows the offset rim and a little of the tire clearance.



And a view of the left to compare.



The spokes on the left side of the rim have just a few millimeters of the tread engaged. It is enough to hold the bike up, but I don't think will be strong enough to ride with. I need to get some longer ones to do the final build.

-x3300

*jgrady1982, Jan 24, 2011:*

All I have to say is...wow

*bikecat, Jan 24, 2011:*

X3300,

Great thread, and even greater work!

One question; how difficult it is to rebuild the X-spokes wheel? Literature on the net makes it sound next to impossible.

Cheers

*NOTICES*

All ORGS design materials are relesed under the Fabricators Design License.

Copyright x3300

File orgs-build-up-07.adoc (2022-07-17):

:url-bmw-frame-gussets: https://www.advrider.com/f/threads/bmw-frame-gussets.638795/
:url-frame-gussets-svg: https://github.com/moto-design/bmw-frame-gussets

:imagesdir: images

:notitle:
:nofooter:

= ORGS Build Up - Page 7

[big]*The ORGS Build Up Project*

*Page 7*

*icebox, Jan 24, 2011:*

All I can say is "if you ever need a job, call, have a small fab shop in paradise"

but our work tends to be repetitious and boring, not near as much fun as building bikes. Have at it, it's fun watching.

*x3300, Jan 30, 2011:*

bikecat said:

Literature on the net makes it sound next to impossible. Click to expand...

Bikecat, everything I post here is genuine and done by my own hand. I try to make it entertaining to read the reports so don't include some details, but nothing is faked nor presented in a misleading way.

-x3300

*x3300, Jan 30, 2011:*

As I mentioned in an earlier post, I didn't like the way my lower shock mount turned out. I decided to cut it off and make a new one. I searched around in the McMaster-Carr catalog for a 12mm ID spherical bearing that would match the M12 shock mount bolt and found one with dimensions 12x30x16 that I thought would work. I also found some 17x30x7 oil seals that had the same OD as the bearing that I thought I could use to keep dirt out of the bearing.

Here's how the old mount I cut off compares to my new design. Once I got the arm installed I found I needed to grind down the smaller front gusset to clear the shock's mounting clevis.



I made the bearing holder from a piece of large mild steel round stock I had. I bored the hole out with this setup to give a press fit to the bearing.



Here's the bearing mount tacked to the swingarm. I made it wide enough to accept the bearing and the two seals on each side of the bearing.



I was thinking to add a box section to the bottom of the swingarm to strengthen it. I cut the sections at the bottom of this photo from a length of mild steel rectangular tube.



I needed to grind a curve in the ends where the box intersects the swingarm tube. It is a little difficult to explain, but to lay out the curve I found a short plastic ring the same diameter as the swingarm tube, and with the plastic ring set into the box section I sighted down the ring and marked the intersection with a Sharpie pen, then ground out the curve with a bench grinder. Here are the parts tacked to the swingarm.



The swingarm all welded together. The box section looks big and heavy, but the tube had a thin wall so it doesn't actually add much weight.



Here's a view of the bottom showing the box section. The rear part is just a little too close to the outer final drive mounting nut to get a socket on the nut. I did a little grinding to make room.



After welding the bearing holder and gussets to the swingarm I found that the bearing holder was distorted enough that the bearing could no longer be pressed in. It took a while to get setup, but I mounted the swingarm on a vertical mill and re-bored the bearing hole.



In retrospect, I think a much better way to do the bearing holder would have been to turn the OD of the holder, but not bore the hole, then weld that un-bored holder to the arm and use my arm fixture to get the arm mounted on the mill to drill and bore the hole.

Here's a side view of the arm with the bearing installed which also shows the shortened front bearing mount gusset.



And a view of the bearing mount. The oil seals press in just outside the bearing.



And a view with the arm installed on the bike.



I still want to make a vent for the arm. I just need to drill and tap a hole in the front of the arm somewhere, but I'll wait until I have the fender, exhaust, and whatever else it needs to clear installed before doing that.

-x3300

*Caddy82rats, Jan 30, 2011:*

SUPERB work thanks for sharing you'r knowlege

*bikecat, Jan 30, 2011:*

x3300 said:

Bikecat, everything I post here is genuine and done by my own hand. I try to make it entertaining to read the reports so don't include some details, but nothing is faked nor presented in a misleading way.

-x3300 Click to expand...

No doubt about that, hence I'm impressed by the way you respoked the wheel so easily! Great stuff.

*mikyheimann, Jan 31, 2011:*

Can you please elaborate on the wheel lacing? I am very proficient at building and truing wheels, I used to race bicycles, and used to rebuild motocross wheels in the 80's. When i had to build my beemer wheels I encountered difficulties, no matter what i did I couldnt decifer the behaviour of the these wheels. After I think 2 days of frustration I decided to aproach it a a machine - I measured all the spokes to be the same length, and counted turns on the nuts, without any attempt at trueing - and got to within BMW spec for these wheels. I wonder If you did it differently, and if so, if you please let us hear a little about it (even though it's much less interesting than all the other amazing stuff you do!).

TIA, Miky

*Rapid Dog, Jan 31, 2011:*

...ohhh I'm so jealous of all ye Fab Bastids!...

O.K., I'm in.

Man this has got to handle Baja better the the stocker GS.

*x3300, Feb 6, 2011:*

mikyheimann said:

Can you please elaborate on the wheel lacing? Click to expand...

mikyheimann, I don't find anything special about these wheels. I follow standard wheel building techniques and just consider the geometry when making adjustments. I have some detail of building a wheel in my post 'Front Wheel'. There is also a dedicated thread that I have added a few comments to here:

https://www.advrider.com/f/threads/gs-wheel-truing.639315/

-x3300

*x3300, Feb 6, 2011:*

Rotary draw bending of tubes has little cross section distortion at the bend, and I thought that it would give the appearance I wanted in the subframe and rear luggage racks. Here's a nice diagram I found that shows several tube bending methods.



I decided to make my own bender so that I would then have the capability to make a bender for any size tube or bend radius I might find I need. A minimal design would need a bending die with an integrated clamp die, a pressure die, and a frame.

I found a large block of mild steel at the scrap yard I thought I could use to make a double 1/2" & 3/4" bending die for a 1 1/2" radius. I cut the block down to a square and drilled a hole in the center so I could bolt it to the left over stock I had used to make my lower shock bearing mount. Here's the piece in the lathe almost ready to be turned down.



Once I got the OD turned down I cut grooves of 1/2" and 3/4". I didn't have any full radius cutting tools so I just ground a few left and right hand turning tools to have the proper radius. I had five tools in all to do the grooves, a common center one and left and right radius ones.

Here's the final cutting of the 3/4" groove. After the block was bolted to the mount I drilled a center hole in the bolt so I could support the right side with the center seen in this photo.



Here's the finished bending die with my mount and center drilled bolt.



To simplify the design I decided to weld the clamp die and a handle directly to the bending die. I cut a clamping strap from a thick wall rectangle tube and welded it to the bending die.



I found some 1" square stock to use for the pressure dies. To mill the slots I bought a 1/2" and a 3/4" ball end mill. Here's the milling of the 3/4" die.



Here's a view of the 1/2" die with a section of tube and the cutter.



I had some rectangle stock left over from my swingarm fixture that used for the frame. I cut these slots to allow adjustment of the pressure die position.



Here are all the finished parts ready for assembly.



And the bender in action. I used some c-clamps to clamp it to this sturdy frame. I put some grease on the pressure die to lubricate it. It doesn't take much to bend 1/2" thin wall tube. 3/4" takes considerably more effort.


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

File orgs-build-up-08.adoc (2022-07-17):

:url-bmw-frame-gussets: https://www.advrider.com/f/threads/bmw-frame-gussets.638795/
:url-frame-gussets-svg: https://github.com/moto-design/bmw-frame-gussets

:imagesdir: images

:notitle:
:nofooter:

= ORGS Build Up - Page 8

[big]*The ORGS Build Up Project*

*Page 8*

*fishkens, Mar 26, 2011:*

As with everything you've done, this is a very nice mod. This has been on the list for my GS (stock swingarm) for some time and I hope to get to it this spring.

*NordieBoy, Mar 29, 2011:*

x3300 said:



You're going to need a bigger tyre than that one...

*x3300, Apr 12, 2011:*

I took the rear wheel apart to do the final build with the proper length spokes. In preparation for powder coating I scrubbed up the rim and hub with a strong detergent and steel wool followed by sand blasting and another detergent scrub and rinse.



The smaller rear rim would just barely fit into the oven I have access to, but I wasn't confident I could get the rim into the oven without jarring the rim and having the loose powder come off, so I decided to use the same setup I used with the front rim to do a partial bake of the rim on the bench to stabilize the coating then I transfered the rim to the oven to do a final bake.



Here's the rim and hub after coating.



I got back in touch with Doug Richardson of The Devon Rim Co. and within a short time 20 spokes 6mm longer than stock arrived. I used the 20 that I had previously ground down shorter for the other side.



There was some interest in my method of building a wheel, so I'll give some more details here. I use a copper based anti-seize to lubricate the stainless spoke threads.


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

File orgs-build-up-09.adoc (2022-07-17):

:url-bmw-frame-gussets: https://www.advrider.com/f/threads/bmw-frame-gussets.638795/
:url-frame-gussets-svg: https://github.com/moto-design/bmw-frame-gussets

:imagesdir: images

:notitle:
:nofooter:

= ORGS Build Up - Page 9

[big]*The ORGS Build Up Project*

*Page 9*

*x3300, May 19, 2012:*

I had been looking around and collecting different kinds of foam samples to mock up and test the seat with. After some trials I found that a base layer of rebond foam with another layer of firm weight upholstery grade open cell foam over it provides enough bottoming protection from the rebond and enough cushion from the open cell. Here's a view of the bare seat pan.
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

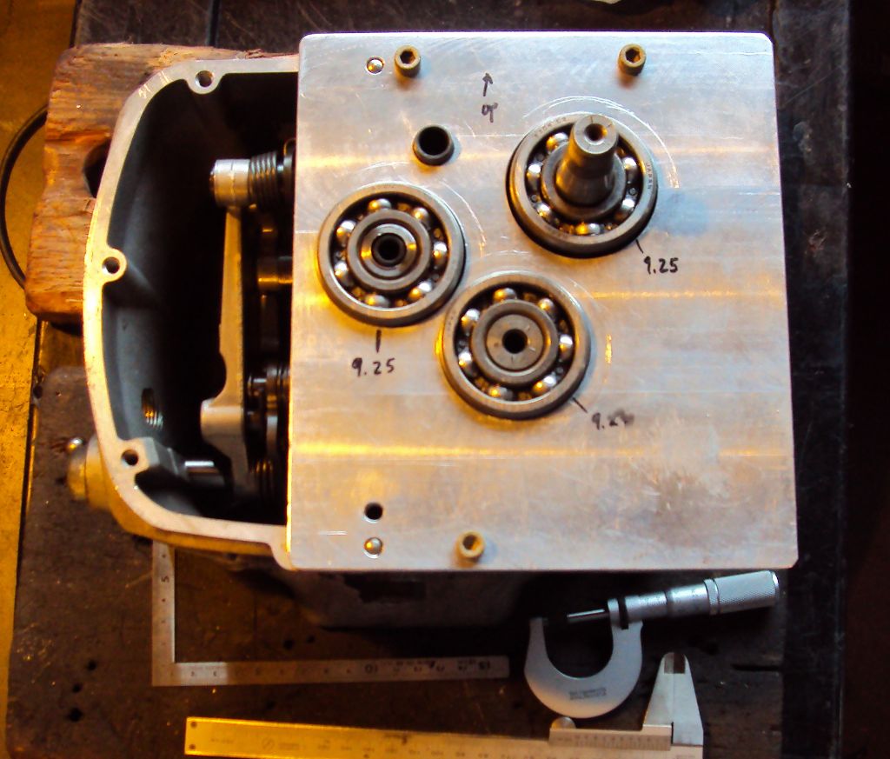
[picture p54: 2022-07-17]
images/23-trans-rebuild/shim-plate.jpg

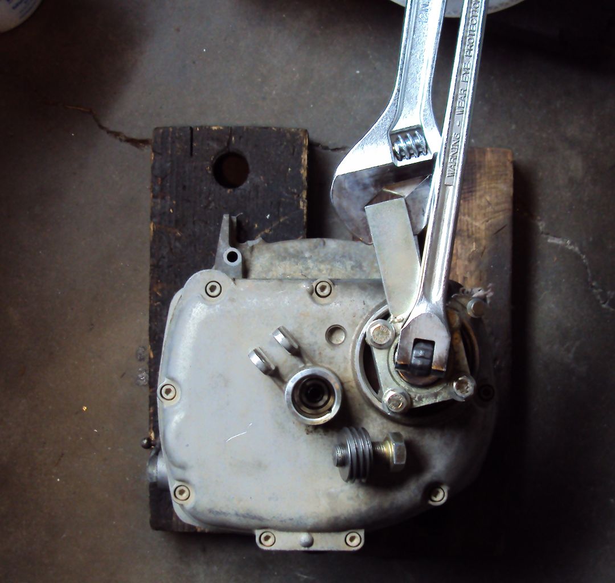
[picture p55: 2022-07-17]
images/23-trans-rebuild/flange-puller.jpg

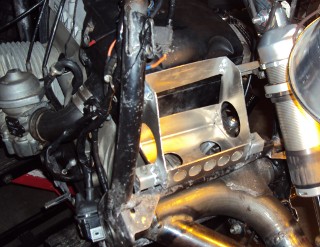
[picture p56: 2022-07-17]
images/33-battery-tray/installed-sm.jpg

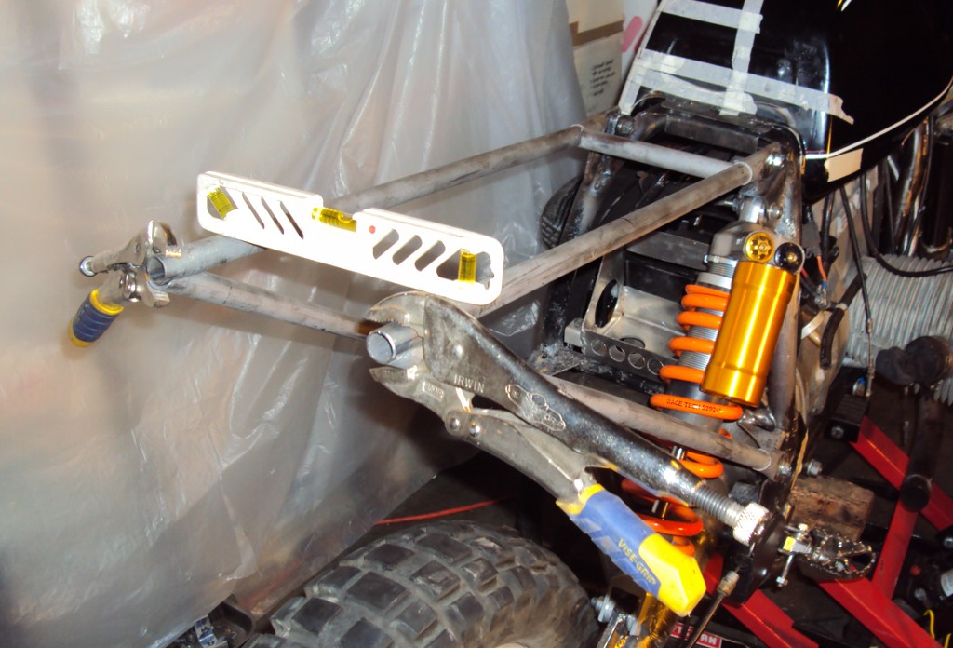
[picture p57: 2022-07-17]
images/35-subframe/weld-setup.jpg

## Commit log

2022-07-17 Add images
    [angle-plate.dxf, battery-tray.dxf, bearing-plug.dxf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]
2022-07-17 bmw-frame-gussets: Add module
